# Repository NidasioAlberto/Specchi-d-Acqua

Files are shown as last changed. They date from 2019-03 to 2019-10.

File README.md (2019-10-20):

# Specchi d'Acqua

[Manifesto team Specchi d'Acqua](Manifesto_team_Specchi_d'Acqua.pdf)

[Modello su Prusa printers](https://www.prusaprinters.org/prints/7135-drone-acquatico)

## Presentazione del progetto

### Introduzione
Il progetto Specchi d’Acqua si pone l’obiettivo di aiutare gli scienziati nello
studio dei cambiamenti climatici. Proponiamo una rete di droni autonomi
che, spostandosi per i mari, monitorano i cambiamenti dovuti al riscaldamento
globale: dall’aumento delle temperature all'innalzamento del livello dell’acqua.
I droni sono in parte costruiti con elementi riciclati per diminuire il loro
impatto ambientale, nell’ottica del riutilizzo di materiali destinati al monouso.

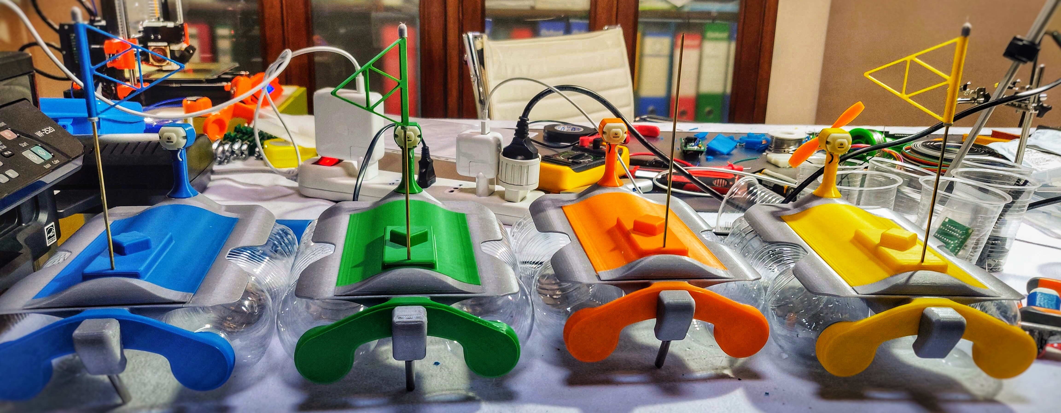
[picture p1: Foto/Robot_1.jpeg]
Robot

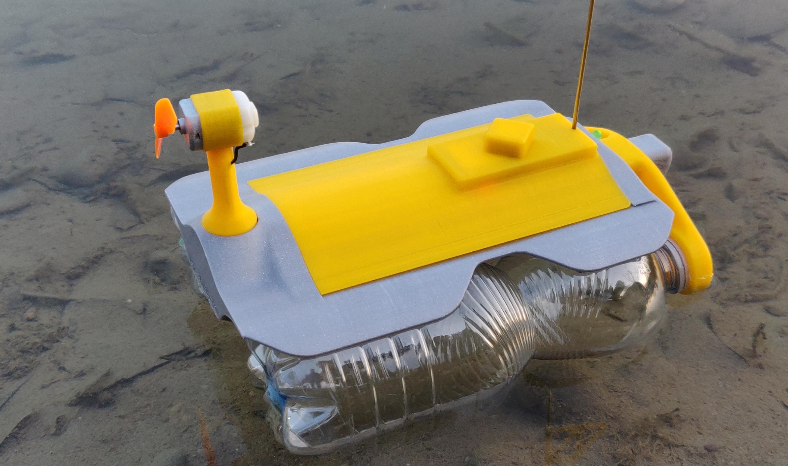
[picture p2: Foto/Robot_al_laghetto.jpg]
Robot al laghetto


**Video:** [prove dei robot](https://youtu.be/X26Ot0CG_ao)

### La squadra

**Video**: [presentazione team](https://youtu.be/9cNglWY3D-Q)

Alberto Nidasio e Matteo Cristini

### Il problema affrontato

**Video**: [Il cambiamento climatico è reale!](https://youtu.be/WMdsdqbVi9s)

Il cambiamento climatico è un grave problema che affligge il nostro pianeta e produce effetti devastanti, molte volte purtroppo imprevedibili, che già oggi possiamo constatare. Il mar Mediterraneo, ad esempio, essendo una zona chiusa sta sperimentando l’impatto di questi cambiamenti più di altre aree del pianeta.
Gli effetti prodotti sono svariati e l’aumento delle temperature (il 2018 è il quarto anno più caldo di sempre) ne è la causa principale. Tra i numerosi problemi c’è la riduzione delle precipitazioni, seppur controintuitiva, che comporta l’aumento della richiesta idrica, soprattutto per uso agricolo (si stima fino al 74%). Aumentano inoltre la diffusione delle malattie e i danni alla salute dovuti alle ondate di calore che ormai caratterizzano le nostre estati.
Il livello dei mari in tutto il mondo sta aumentando e le località costiere corrono un grande rischio. Invece le alte temperature danneggiano i coralli e alterano i delicati ecosistemi marini.
Lo studio da parte degli scienziati di tutti questi fenomeni interconnessi e altamente complessi si basa sulla disponibilità di dati e analisi il più possibile accurati e distribuiti al fine di poter, non solo capire il perché si sia verificato un fenomeno, ma anche per prevedere possibili disastri.

### La nostra soluzione

**Video**: [Presentazione del progetto](https://youtu.be/HUvQelgl1Qg)

La raccolta dati è fondamentale prima di ogni azione mirata: la si fa per un’analisi di mercato, per l’acquisto di un giocatore, perfino per un attacco informatico. Impiegarla per studiare i fenomeni naturali è però più complesso e costoso, infatti richiede attrezzature all’avanguardia non sempre recuperabili.
Noi abbiamo la soluzione! Il nostro progetto consiste in una flotta di droni acquatici, realizzati con materiali riciclati, in grado di distribuirsi in autonomia in un’area prestabilita, tornando alla base a fine missione. Grazie a un modulo GPS installato su ciascuno di essi, i robot potranno capire dove si trovano e mantenere la posizione nonostante le correnti. I droni potranno essere equipaggiati con diversi sensori per monitorare qualunque tipo di dato sia richiesto dagli analisti e, attraverso un sistema di comunicazione wireless, saranno in grado di trasmettere i dati in tempo reale alla base, associandoli con la posizione recuperata dal GPS.I prototipi che abbiamo preprato hanno molti aspetti innovativi. La costruzione dello scafo utilizza bottigliette di plastica e questo ci permette di recuperare quello che altrimenti sarebbe un rifiuto abbandonato.
Inoltre sia il codice che i design del robot saranno open-source permettendo così a chiunque di migliorare il progetto apportando nuove modifiche.
Il robot utilizza anche parti stampate in 3D. Questi componenti sono realizzati su misura, permettendo a ogni modello di essere equipaggiato con diversi sensori e batterie, per adattarsi alle esigenze del momento.

## Descrizione tecnica: drone

### Lo scafo

Il drone è composto da uno scafo realizzato con bottigliette di plastica tenuto assieme da una struttura progettata a **CAD** e realizzata con **stampante 3D**, adattabile in base alle esigenze e che contiene:
- i motori, per la propulsione e l'orientamento dell'elica;
- i sensori;
- il microcontrollore, che raccoglie i dati, gestisce la comunicazione e coordina il movimento;
- la sezione alimentazione che fornisce elettricità ai vari componenti.

I modelli del drone sono disponibili [qui](Modelli).

**Video:** [Esplosione modello](https://youtu.be/hAqc2swxTDc)

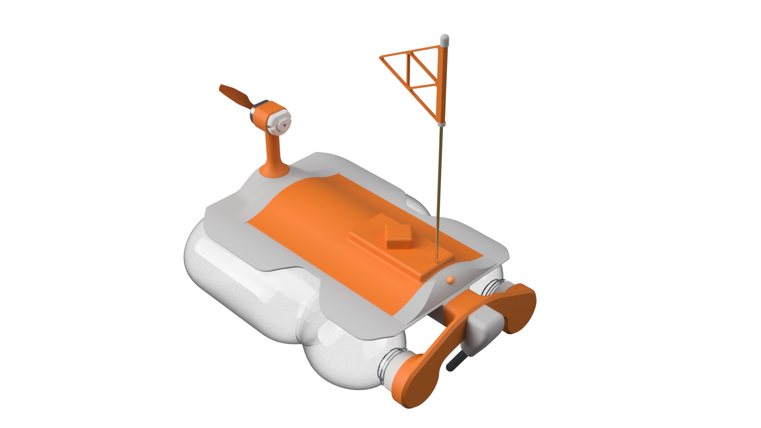
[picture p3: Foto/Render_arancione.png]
Foto modello


### Processore, sensori, alimentazione e schemi tecnici

La raccolta dei dati è gestita dal microcontrollore ESP8266 che è stato scelto per la sua disponibilità a un prezzo modesto e per le numerose funzionalità offerte. Infatti, non solo dispone di numerose porte I/O, ma anche di un trasmettitore wifi che metterà in comunicazione i droni tra di loro. Per quanto riguarda la scelta dei sensori, il progetto prevede piena libertà nella loro selezione in base alle esigenze del caso. Per questo prototipo abbiamo impiegato sensori di temperatura (sia in aria che in acqua, con una sonda da immergere), umidità e un modulo gps. Verrà quindi registrata la posizione del robot non solo per permettergli di distribuirsi nell’area designata, ma anche per associarla ai dati dei sensori.
Per l’elettronica di bordo sono stati previsti diversi metodi di alimentazione:
- tramite pile stilo da sostituire regolarmente (metodo attuale);
- tramite batteria ricaricabile al litio: è previsto siano necessarie due celle
assieme a un circuito di ricarica dedicato; Sul coperchio è possibile installare un pannello solare di dimensioni contenute in grado di ricaricare il gruppo batterie del robot.

#### Processore e sensori

L'Esp8266 ci permette di utilizzare i sensori **DHT11** (temperatura e umidità aria), **DS18B20** (Sonda temperatura acqua) e il modulo gps **GT-U7**. Per collegare tutti questi componenti abbiamo preparato una scheda millefori che verrà alloggiata nel coperchio dello scafo per una manutenzione facile e semplice. Una volta finalizzato il design potremo creare un vera e propria **PCB** con componenti **SMT**.

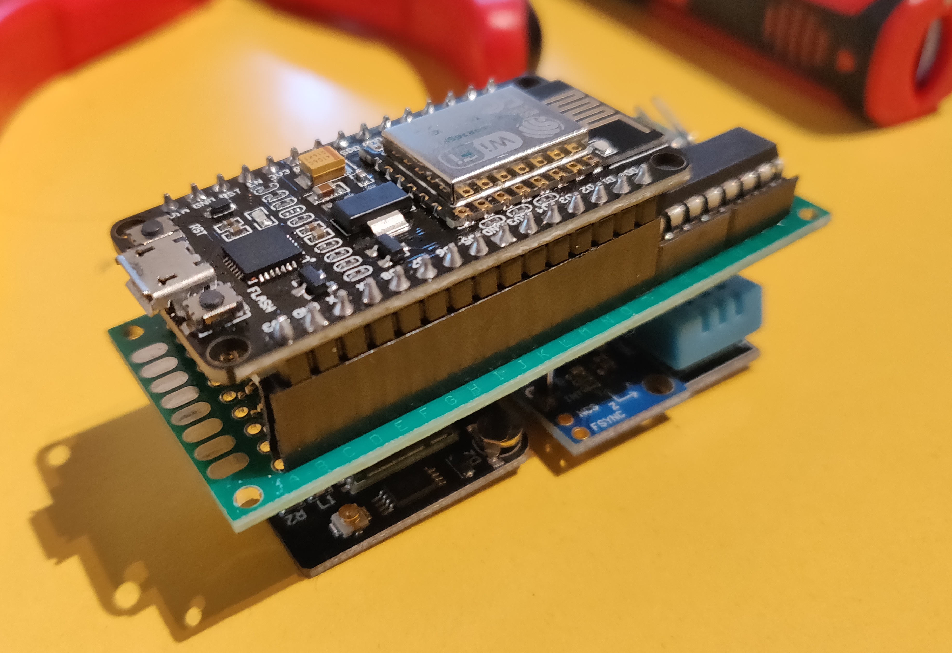
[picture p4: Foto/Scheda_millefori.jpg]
Scheda millefori


#### Alimentazione

Per alimentare la scheda e i motori abbiamo utilizzato due set di batterie separati. Il primo, composto da 4 batteria AA fornisce elettricità al motore DC che muove l'elica, e il secondo, formato da 6 batterie AAA, che alimenta l'elettronica e il motore passo passo che inclina l'elica.
Questo evita che, nel caso di cali di tensione all'elettronica dovuti all'avvio del motore o se si scaricano le batterie del motore DC, il drone perda il segnale e non risponda più ai programmi.

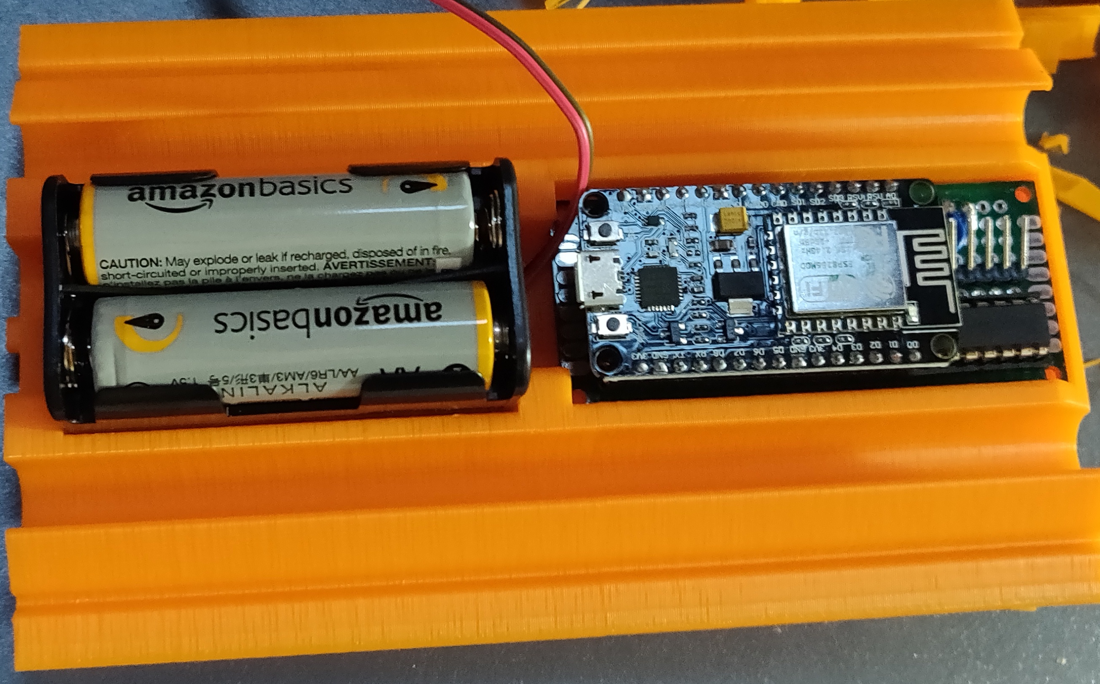
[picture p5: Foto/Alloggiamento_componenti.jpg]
Foto alloggiamento batterie


#### Schemi tecnici

![Schema millefori]()

## Descrizione tecnica: collettore

I droni, distribuite su una vasta zona, avranno bisogno di un sistema di comunicazione affidabile a lunga distanza. In base alle dimensioni dell’area su cui devono essere distribuiti abbiamo valutato diverse soluzioni:
- Per comunicazioni nell’ordine delle decine di chilometri sono disponibili moduli **LoRa** (Long Range), anche ad un prezzo ridotto, che permettono un collegamento a maglia, estendendo così considerevolmente la rete, a patto che ci sia un numero sufficiente di nodi.
- Nel caso invece si voglia lavorare su zone più ampie, esigendo anche un livello di affidabilità superiore, si potrà sfruttare, nei prossimi anni, la rete satellitare **Starlink**, una costellazione di 12.000 satelliti che SpaceX sta sviluppando per portare l’accesso ad internet in qualunque area del pianeta. Questo offrirebbe una connessione indipendente per ciascun drone eliminando la possibilità che alcuni possano rimanere isolati.

Per il prototipo abbiamo utilizzato una rete **Wifi** che collega droni e collettore con la possibilità di essere estesa con dei ripetitori. Lo stesso sistema che abbiamo sviluppato, che utilizza il protocollo **MQTT** (per l'invio dei dati)  e **TCP** (per il controllo da remoto), potrà essere implementat con la rete cellurare.

Per il collettore, ovvero il server a terra che memorizza i dati, abbiamo utilizzato un **Raspberry pi**.

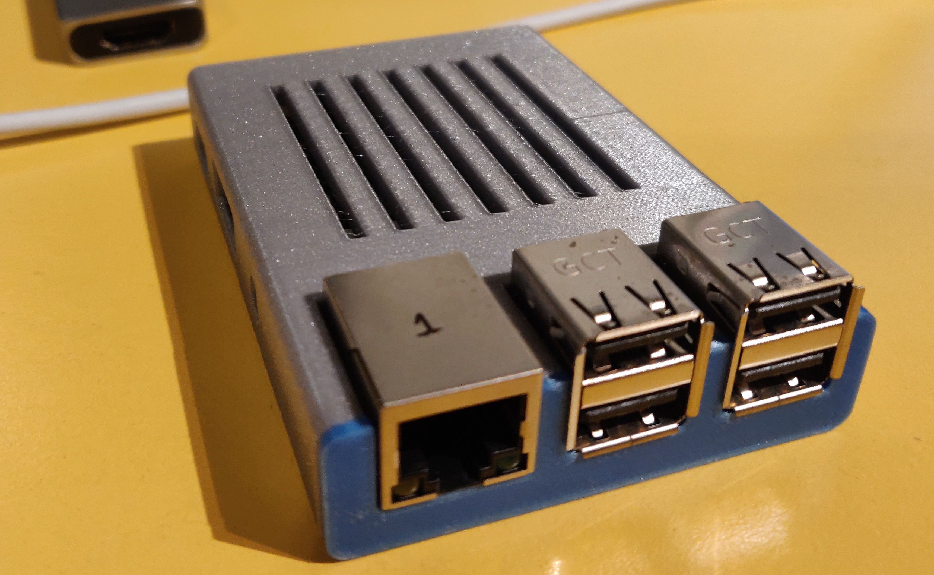
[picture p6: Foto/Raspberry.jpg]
Foto raspberry


## Software

Il collettore (S.O. Linux) implementa un broker **Mosquitto**, un server **Sql**, un server **HTTP** con un sito web e un processo per sincronizzare i dati web che forniscono i servizi necessari per la comunicazione, il salvataggio e la visualizzazione dei dati.

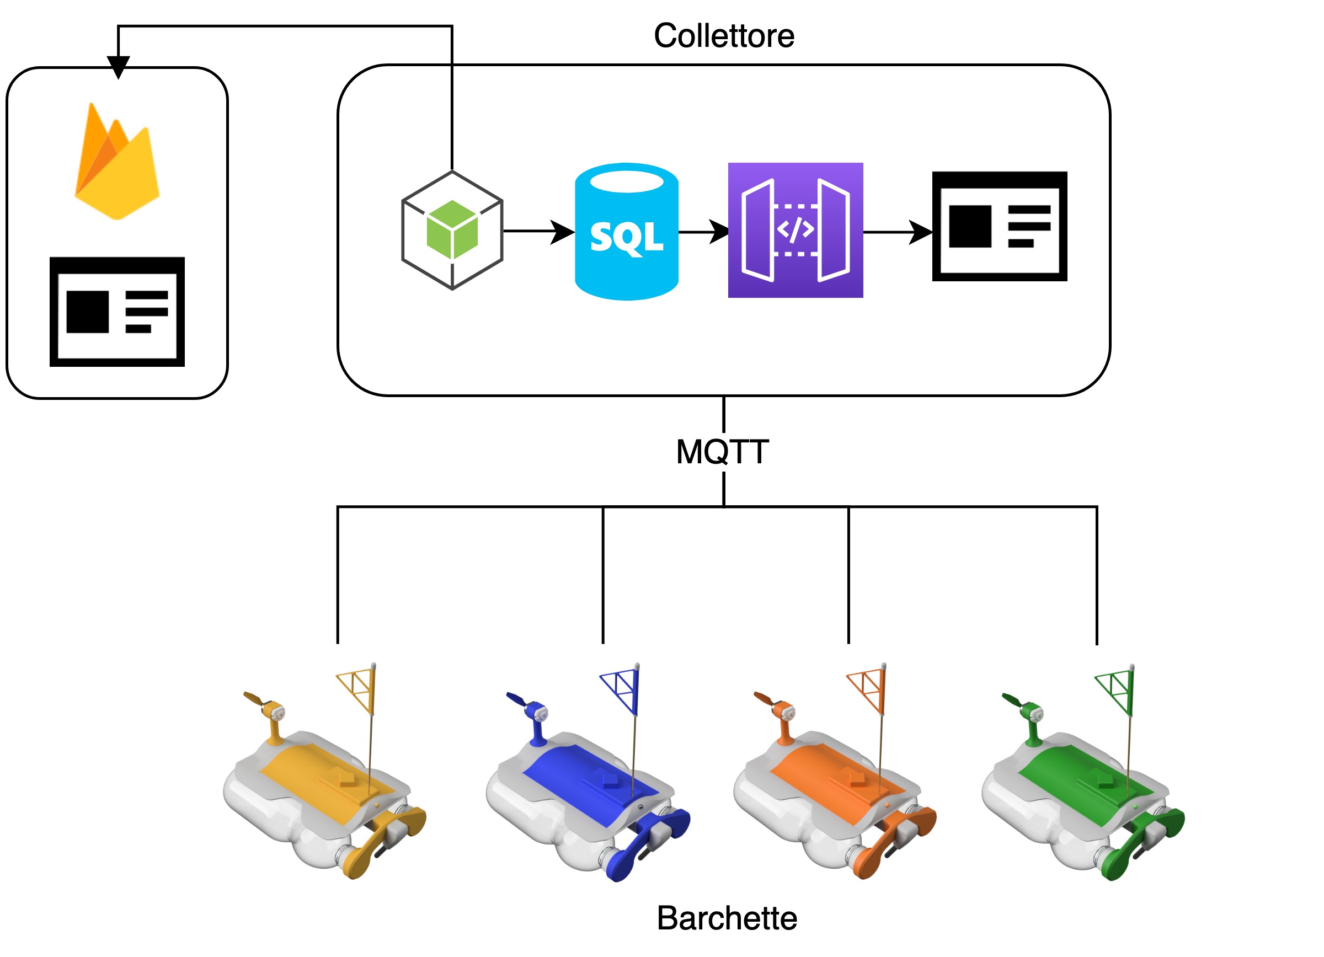
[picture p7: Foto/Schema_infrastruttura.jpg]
Schema imfrastruttura


### Broker Mosquitto

Per la comunicazione tra droni e collettore abbiamo utilizzato il protocollo ***MQTT*** che ci permette un'affidabilità della comunizatione superiore (QOS 2) e riduzione della dimensione dei messaggi. Questo è fornito dal popolare broker **Mosquitto** a cui si collegheranno i droni come publisher e il server.

### Server SQL

Il server **SQL** (MariaDB) è organizzato in 4 tabelle principali:
- **Droni**: contiene la lista di tutte i droni prodotti;
- **Sensori**: la lista di tutti i sensori utlizzati (esclusi GPS e bussola);
- **Record**: dove vengono salvati i dati principali di un record come posizione, data, ora e id del drone;
- **Dati sensori**: permette di memorizzare i valori di ciascun sensore rilevati in un record (questa è una tabella separata perchè i droni potrebbero non avere tutti la stessa configurazione).

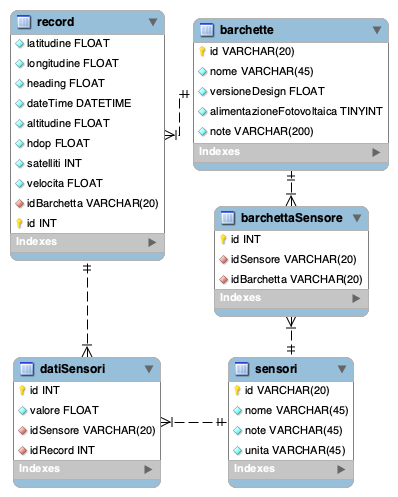
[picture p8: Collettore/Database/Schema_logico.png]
Schema logico


### Server HTTP

Questo servizio fornisce delle **API REST** che il sito web, sempre messo a disposizione da questo server, utilizza per mostrare i dati.

## Olimpiadi

### Giorno 1
**Video:** [time-lapse giorno 1](https://youtu.be/L8EZxuS9RvE), [time-lapse giorno 2](https://youtu.be/6cRvtolq8c4)

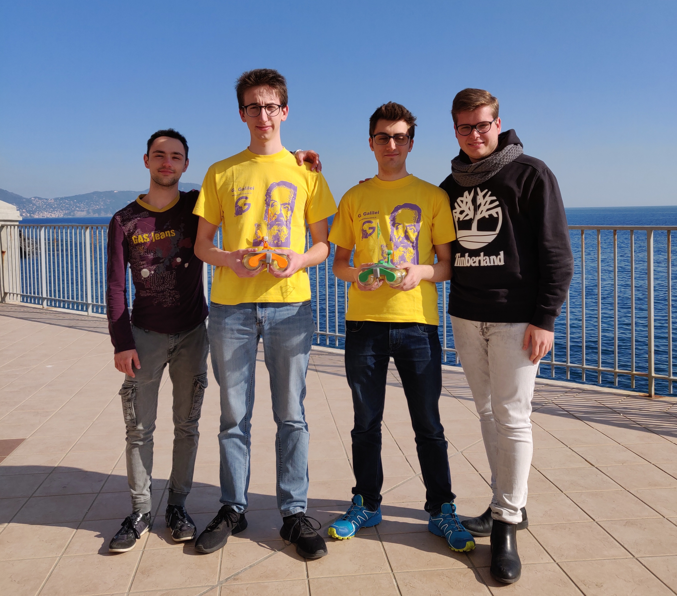
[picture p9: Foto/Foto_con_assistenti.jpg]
Foto con amici


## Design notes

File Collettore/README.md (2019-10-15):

# Impostazione raspberry collettore

## Setup access point

Per impostare il raspberry come access point è possibile seguire questa guida: [Tutorial](https://www.raspberrypi.org/documentation/configuration/wireless/access-point.md)

## Setup MQTT - server mosquitto

[Tutorial](https://appcodelabs.com/introduction-to-iot-build-an-mqtt-server-using-raspberry-pi)

## Setup server SQL

[Tutorial](https://pimylifeup.com/raspberry-pi-mysql/)

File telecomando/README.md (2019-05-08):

# telecomando

A new Flutter project.

## Getting Started

This project is a starting point for a Flutter application.

A few resources to get you started if this is your first Flutter project:

- [Lab: Write your first Flutter app](https://flutter.io/docs/get-started/codelab)
- [Cookbook: Useful Flutter samples](https://flutter.io/docs/cookbook)

For help getting started with Flutter, view our 
[online documentation](https://flutter.io/docs), which offers tutorials, 
samples, guidance on mobile development, and a full API reference.

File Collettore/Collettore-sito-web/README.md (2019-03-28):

# CollettoreSitoWeb

This project was generated with [Angular CLI](https://github.com/angular/angular-cli) version 7.3.4.

Aggiunta la lib. angular material
Aggiunta la lib. angularfire2
Aggiunta la lib. ng2chart
Aggiunta la lib. chart.js

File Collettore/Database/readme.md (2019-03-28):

# Database barchette
Alberto Nidasio - Stefano Vassallo

[PDF presentazione 😄](Presentazione_database_barchette.pdf)

## Problema da risolvere
Il team Specchi d’Acqua, che parteciperà alle prossime olimpiadi di robotica a Genova, ha bisogno di salvare i dati ambientali raccolti dalle proprie barchette (temperatura, umidità, ecc...).

## Casi d'uso
Casi d'uso

## Struttura della soluzione
- Database
- Server REST
- Sito web

## Schema database
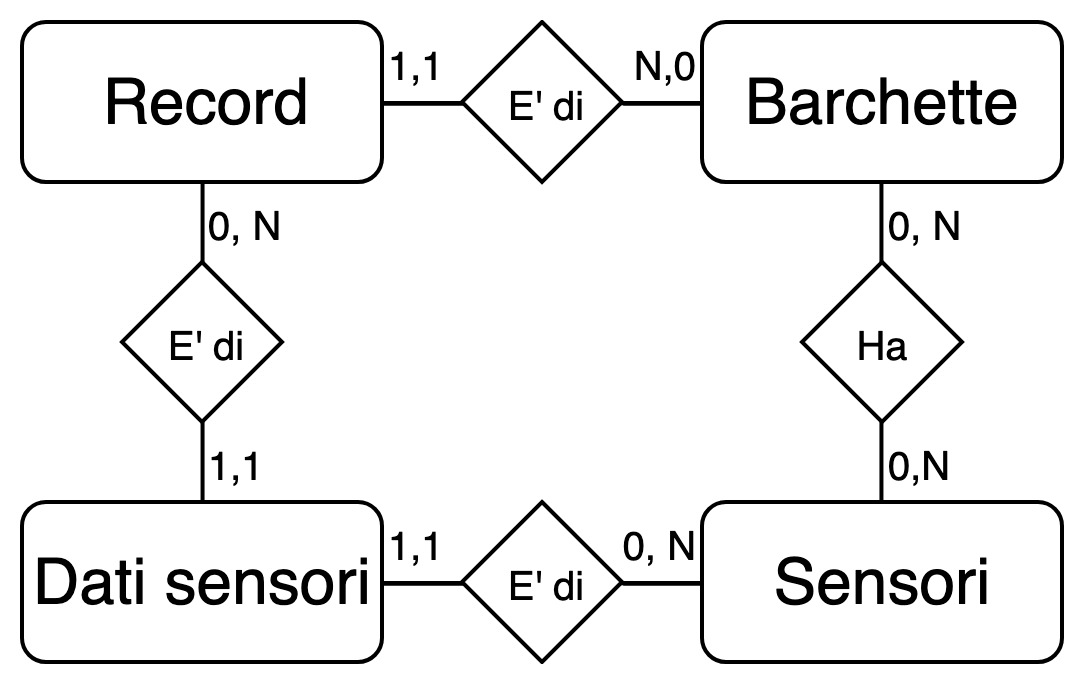
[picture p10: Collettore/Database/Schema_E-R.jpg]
Schema E/R

Schema logico

## Codice server
Utilizzo di NodeJs per l'applicazione server che, oltre alle API REST mette a disposizione il sito web

[Esempio codice server](Server/server.ts)
```typescript
//preparo express
const app = express()
app.use(express.json())
app.use(cors({origin: '*'}))

//rendo disponibile la pagina web nella root dell'url
app.use('/', express.static('website'))

//SEZIONE RECORD

//lista record con i dati dei sensori
app.get('/api/record', async (req, res) => {
    console.log(req.method, req.url, req.query, req.body)

    try {
        return res.send(await database.ottieniRecord(req.query.limite))
    } catch(errore) {
        return res.status(500).send(errore.message)
    }
})
```

## Codice client
Pagina web realizzata con Boostrap e JQuery

[Esempio metodo GET](Server/website/code.js)
```javascript
//funzione per caricare le barchette nella tabella
function caricaBarchette() {
    const http = new XMLHttpRequest()
    const url = 'http://localhost/api/barchette'
    http.open('GET', url)
    http.onload = (e) => {
        var data = JSON.parse(http.responseText)
        $('#tabella-barchette').bootstrapTable({
            columns: [{
                    field:'id',
                    title: '#'
                }, {
                    field:'nome',
                    title: 'Nome'
                }, {
                    field:'versioneDesign',
                    title: 'V. Design'
                }, {
                    field:'alimentazioneFotovoltaica',
                    title: 'Fotovoltaico'
                }, {
                    field:'note',
                    title: 'Note'
                }],
            data
        })
    }
    http.send()
}
```
[Esempio metodo POST](Server/website/code.js)
```javascript
//funzione per registrare un nuovo sensore
function aggiungiSensore() {
    let id = document.getElementById('sensore-id').value
    let nome = document.getElementById('sensore-nome').value
    let note = document.getElementById('sensore-nota').value
    let unita = document.getElementById('sensore-unita').value

    //controllo i dati
    if(id == '' || nome == '' || note == '' || unita == '') {
        //mostro un avviso all'utente
        alert('Compilare tutti i campi!')
    } else{
        const http = new XMLHttpRequest()
        const url = 'http://localhost/api/sensori'
        http.open('POST', url)
        http.setRequestHeader('Content-Type', 'application/json')

        var sensore = { id, nome, note, unita }

        http.onload = (e) => {
            document.getElementById('sensore-id').value = ''
            document.getElementById('sensore-nome').value = ''
            document.getElementById('sensore-nota').value = ''
            document.getElementById('sensore-unita').value = ''
        }

        http.send(JSON.stringify(sensore))
    }	
}
```

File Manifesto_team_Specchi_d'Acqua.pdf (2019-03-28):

# Missione: Specchi d'Acqua

Scuola: IIS G. Galilei Crema Docente Coach: Lini Patrizia Nome Squadra: Specchi d’Acqua di Cristini Matteo, Nidasio Alberto

Ambiente di intervento: Acqua Link al video: Presentazione della Squadra (https://www.youtube.com/watch?v=9cNglWY3D-Q&list=PL8SoLGSAr36Su3RwwoVQFDCZ6iDOUV9Au&index=2) Link al video: Presentazione del Problema (https://youtu.be/WMdsdqbVi9s) Link al video: Presentazione del Progetto (https://youtu.be/HUvQelgl1Qg)

Indice dei contenuti

- Introduzione e vincoli di progetto
- Presentazione del problema da risolvere
- Descrizione della soluzione
- Presentazione del robot
- Schemi tecnici
- Elettronica
- Programmazione
- Conclusioni

Introduzione
Il progetto Specchi d’Acqua si pone l’obiettivo di aiutare gli scienziati nello studio dei cambiamenti climatici. Proponiamo una rete di barche autonome che, spostandosi per i mari, monitorano i cambiamenti dovuti al riscaldamento globale: dall’aumento delle temperature all'innalzamento del livello dell’acqua. Le barche sono in parte costruite con elementi riciclati per diminuire il loro impatto ambientale, nell’ottica del riutilizzo di materiali destinati al monouso.

Presentazione del problema da risolvere
Il cambiamento climatico è un grave problema che affligge il nostro pianeta e produce effetti devastanti, molte volte purtroppo imprevedibili, che già oggi possiamo constatare. Il mar Mediterraneo, ad esempio, essendo una zona chiusa sta sperimentando l’impatto di questi cambiamenti più di altre aree del pianeta.
Gli effetti prodotti sono svariati e l’aumento delle temperature (il 2018 è il quarto anno più caldo di sempre) ne è la causa principale. Tra i numerosi problemi c’è la riduzione delle precipitazioni, seppur controintuitiva, che comporta l’aumento della richiesta idrica, soprattutto per uso agricolo (si stima fino al 74%). Aumentano inoltre la diffusione delle malattie e i danni alla salute dovuti alle ondate di calore che ormai caratterizzano le nostre estati. Il livello dei mari in tutto il mondo sta aumentando e le località costiere corrono un grande rischio. Invece le alte temperature danneggiano i coralli e alterano i delicati ecosistemi marini.
Lo studio da parte degli scienziati di tutti questi fenomeni interconnessi e altamente complessi si basa sulla disponibilità di dati e analisi il più possibile accurati e distribuiti al fine di poter, non solo capire il perché si sia verificato un fenomeno, ma anche per prevedere possibili disastri.

Descrizione della soluzione
La raccolta di dati è fondamentale prima di ogni azione mirata: la si fa per un’analisi di mercato, per l’acquisto di un giocatore, perfino per un attacco informatico. Impiegarla per studiare i fenomeni naturali è però più complesso e costoso, infatti richiede attrezzature all’avanguardia non sempre recuperabili.
Noi abbiamo la soluzione! Ed è la migliore per raccogliere dati ambientali sui mari. Il nostro progetto consiste in una flotta di droni acquatici, realizzati con materiali riciclati, in grado di distribuirsi in autonomia in un’area prestabilita, tornando alla base a fine missione. Grazie a un modulo GPS installato su ciascuno di essi, i robot potranno capire dove si trovano e mantenere la posizione nonostante le correnti. I droni potranno essere equipaggiati con diversi sensori per monitorare qualunque tipo di dato sia richiesto dagli analisti e, attraverso un sistema di comunicazione wireless, saranno in grado di trasmettere i dati in tempo reale alla base, associandoli con la posizione recuperata dal GPS.

Presentazione del robot
Come detto al punto precedente stiamo realizzando una flotta di droni il cui obiettivo principale è quello di aiutare nella raccolta dati. I prototipi che stiamo preparando hanno molti aspetti innovativi. La costruzione dello scafo utilizza bottigliette di plastica e questo ci permette di recuperare quello che altrimenti sarebbe un rifiuto abbandonato.
Inoltre sia il codice che i design del robot saranno open-source permettendo così a chiunque di migliorare il progetto apportando nuove modifiche.
Il robot utilizza anche parti stampate in 3D. Questi componenti sono realizzati su misura, permettendo a ogni modello di essere equipaggiato con diversi sensori e batterie, per adattarsi alle esigenze del momento.
La guida è autonoma; i droni, una volta “liberati”, si distribuiscono e iniziano la raccolta dati, comunicando le letture dei sensori a un concentratore che si trova a terra, responsabile poi dell’immagazzinamento dei dati e della loro analisi.

Schemi tecnici
Lo schema tecnico proposto rappresenta una versione provvisoria dei componenti dell’elettronica di bordo.

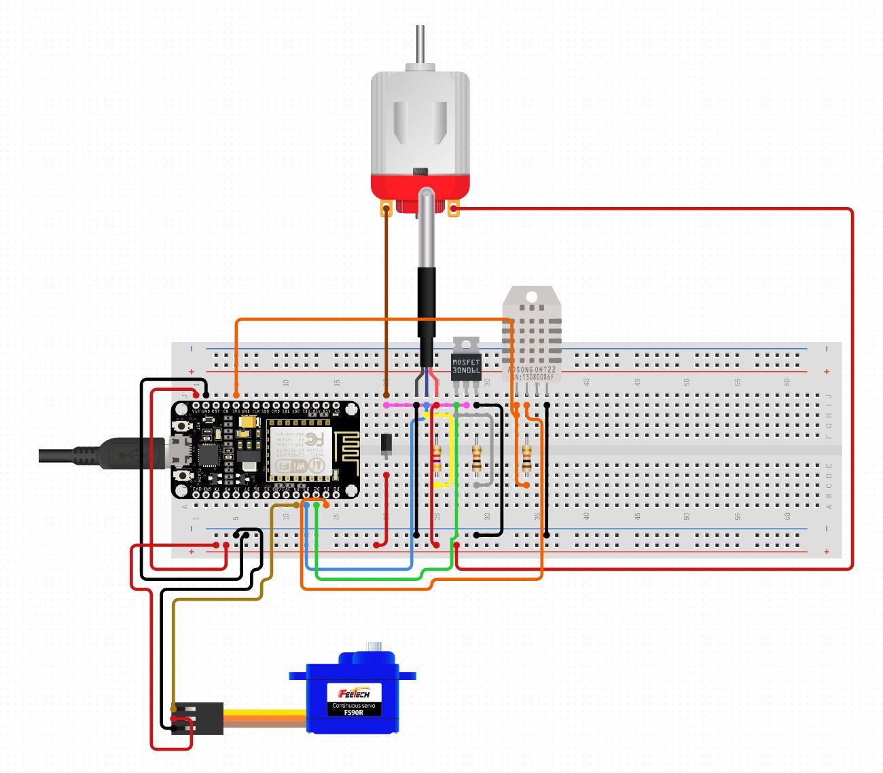
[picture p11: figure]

Elettronica e costruzione - Lo scafo
Il drone è composto da uno scafo realizzato con bottigliette di plastica tenuto assieme da una struttura realizzata con stampante 3D, adattabile in base alle esigenze e che contiene:
- i motori, per la propulsione e il timone;
- i sensori;
- il microcontrollore, che raccoglie i dati,

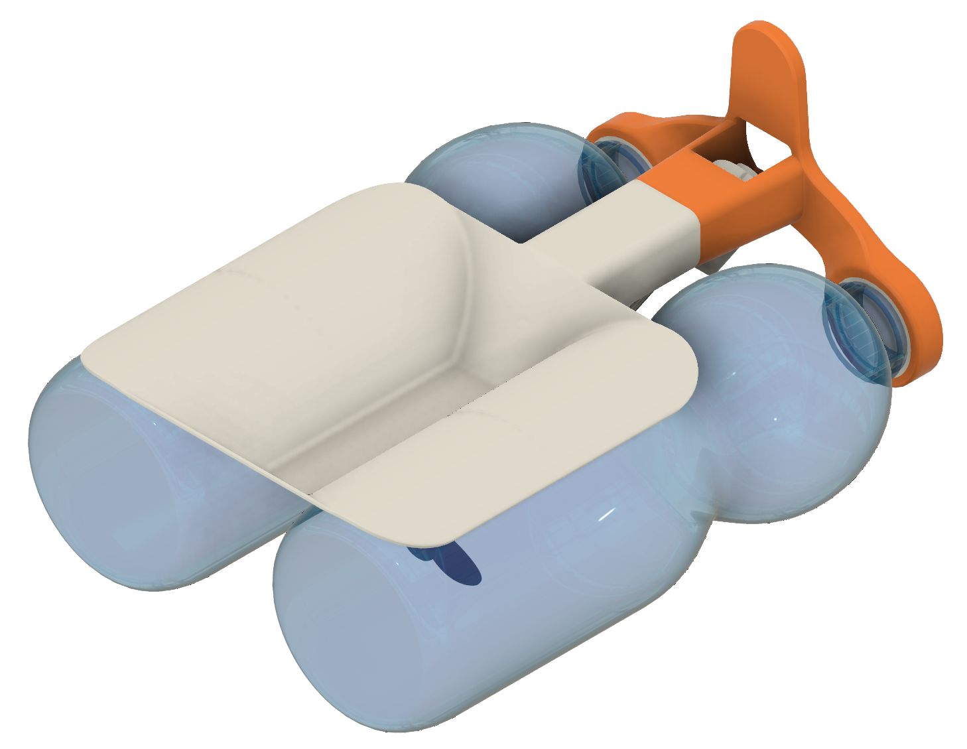
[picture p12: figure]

gestisce la comunicazione e coordina il movimento;
- la sezione alimentazione che procura elettricità ai vari componenti e ricarica le batterie con pannelli fotovoltaici.

Elettronica e costruzione - Processore e
sensori
La raccolta dei dati è gestita dal microcontrollore ESP8266 che è stato scelto per la sua disponibilità a un prezzo modesto e per le numerose funzionalità offerte.
Infatti, non solo dispone di numerose porte
I/O, ma anche di un trasmettitore wifi che
metterà in comunicazione i droni tra di loro.

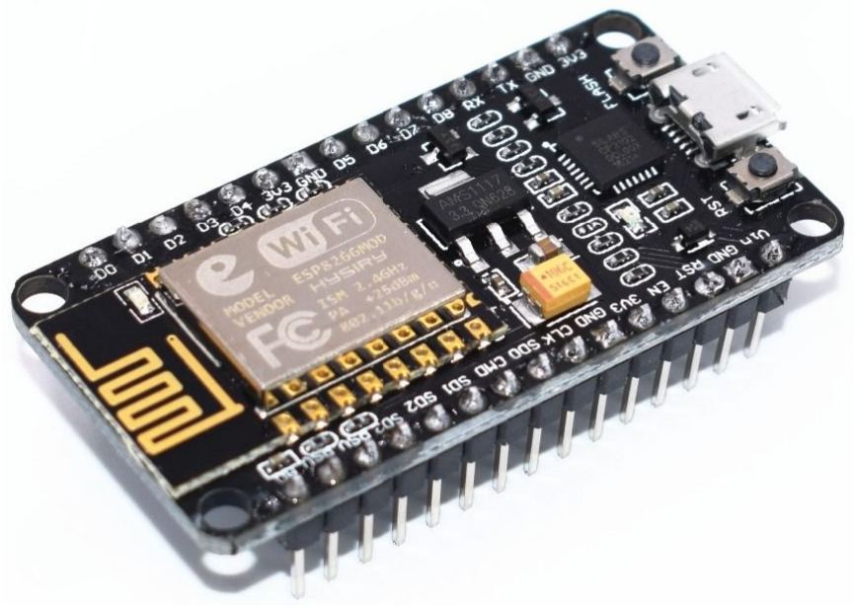
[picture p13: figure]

Per quanto riguarda la scelta dei sensori, il progetto prevede piena libertà nella loro selezione in base alle esigenze del caso. Per i primi prototipi e test verranno impiegati sensori di concentrazione CO2 e di temperatura (sia in aria che in acqua, con una sonda da immergere) mentre sono necessari due moduli: bussola e gps.
Verrà quindi registrata la posizione del robot non solo per permettergli di distribuirsi nell’area designata, ma anche per associarla ai dati dei sensori.

Elettronica e costruzione - Alimentazione
Per l’elettronica di bordo sono stati previsti diversi metodi di alimentazione:
- tramite quattro pile stilo da sostituire regolarmente;
- tramite batteria ricaricabile al litio: è previsto siano necessarie due celle assieme a un circuito di ricarica dedicato.

Sulla piattaforma dei sensori è possibile installare un pannello solare di dimensioni contenute in grado di ricaricare il gruppo batterie del robot.

Programmazione, codice e comunicazione
I droni marini, distribuiti su una vasta zona, avranno bisogno di un sistema di comunicazione affidabile a lunga distanza. In base alle dimensioni dell’area su cui devono essere distribuiti abbiamo valutato diverse soluzioni.
Per comunicazioni nell’ordine delle decine di chilometri sono disponibili moduli LoRa (Long Range), anche ad un prezzo ridotto, che permettono un collegamento a maglia, estendendo così considerevolmente la rete, a patto che ci sia un numero sufficiente di droni.
Nel caso invece si voglia lavorare su zone più ampie, esigendo anche un livello di affidabilità superiore, si potrà sfruttare, nei prossimi anni, la rete satellitare Starlink, (https://en.wikipedia.org/wiki/Starlink_(satellite_constellation)) una costellazione di 12.000 satelliti che SpaceX sta sviluppando per portare l’accesso ad internet in qualunque area del pianeta. Questo offrirebbe una connessione indipendente per ciascun drone eliminando la possibilità che alcuni possano rimanere isolati.

Conclusioni
Il cambiamento del nostro pianeta è reale e solo un attento studio dei fenomeni e dell’ambiente ci permetterà di capire e prevenire numerosi disastri. In questo la tecnologia è il miglior alleato che si possa avere dalla propria parte e noi del team “Specchi d’Acqua”, sentendo molto questo problema, ci proponiamo di sfruttare i nostri studi odierni e futuri per contribuire alla salvaguardia del patrimonio di bellezze che la terra offre.

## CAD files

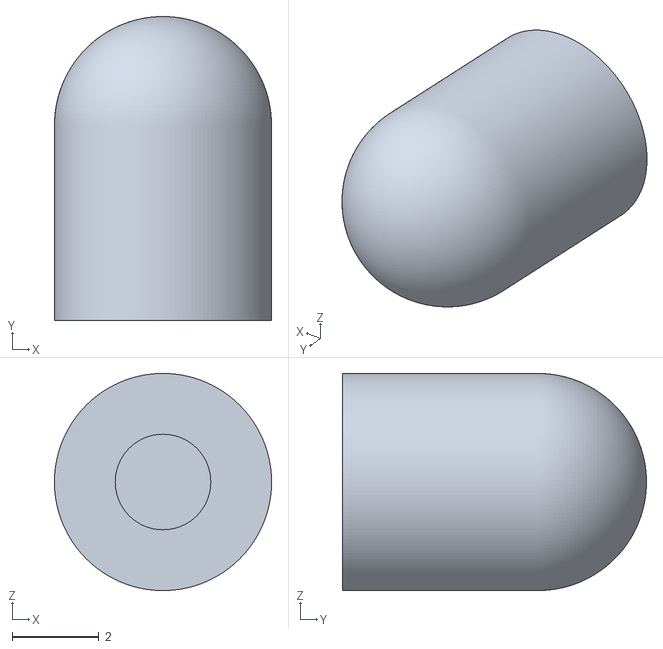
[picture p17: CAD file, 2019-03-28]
Modelli/Parti/Supporto superiore bandierina.stl
5.00 x 7.00 x 5.00

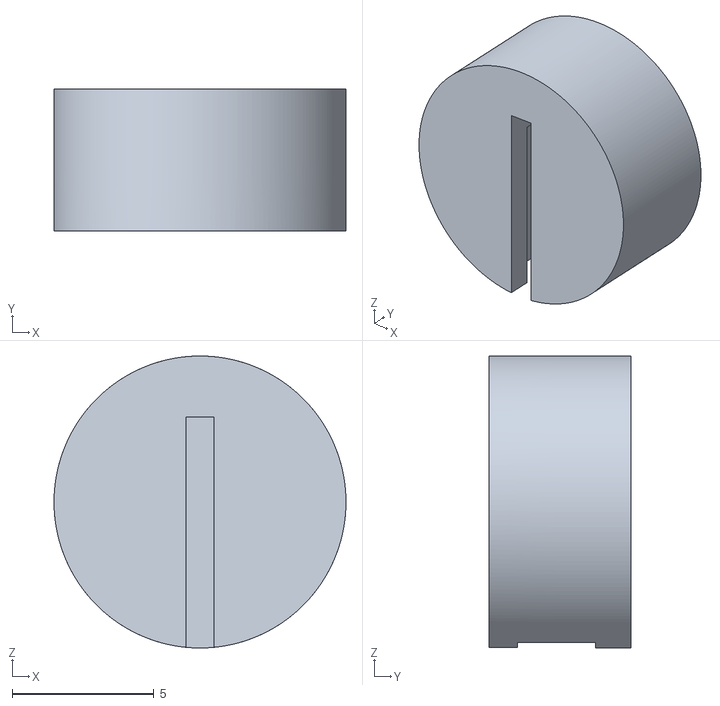
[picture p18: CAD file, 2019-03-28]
Modelli/Parti/Contatto batterie AAA pt1.stl
10.3 x 5.00 x 10.3

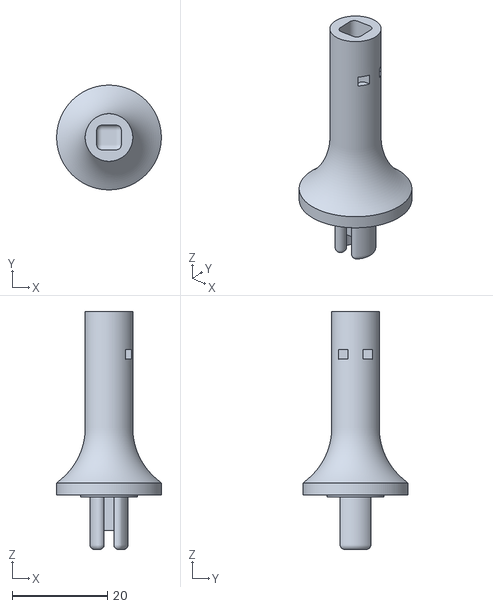
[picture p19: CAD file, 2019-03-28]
Modelli/Parti/Asse motore.stl
22.0 x 22.0 x 50.0

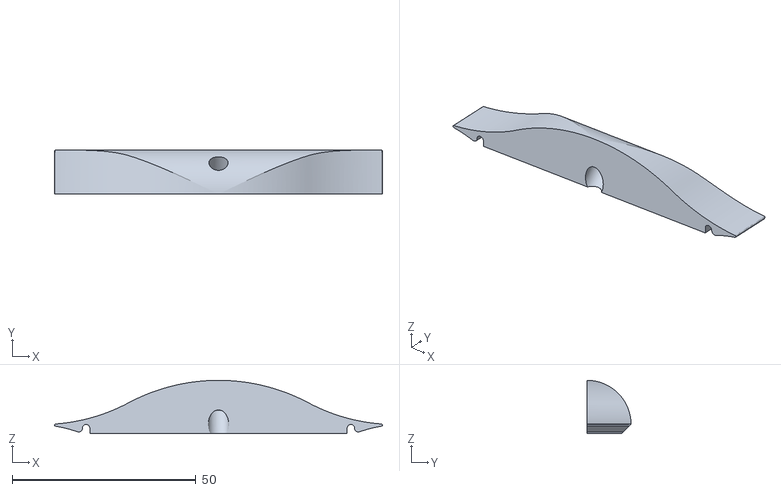
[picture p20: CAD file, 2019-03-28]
Modelli/Parti/Supporto coperchio.stl
89.2 x 12.0 x 14.5

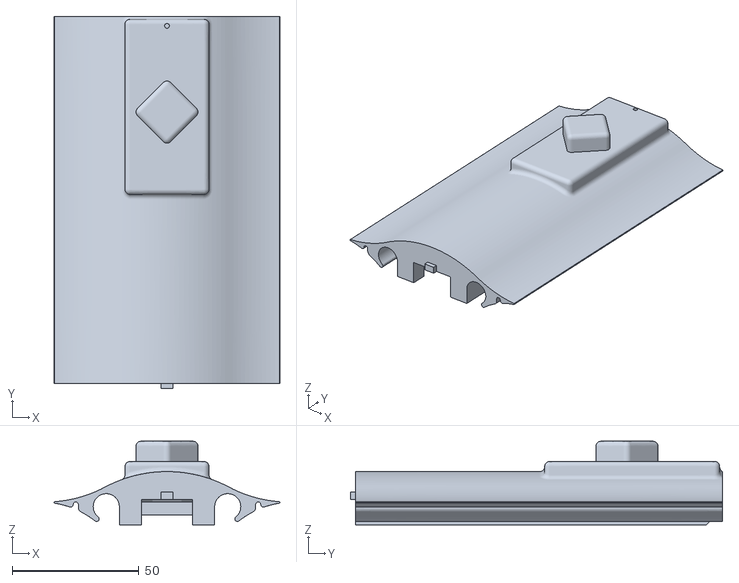
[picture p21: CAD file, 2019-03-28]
Modelli/Parti/Coperchio.stl
89.2 x 147.0 x 33.0

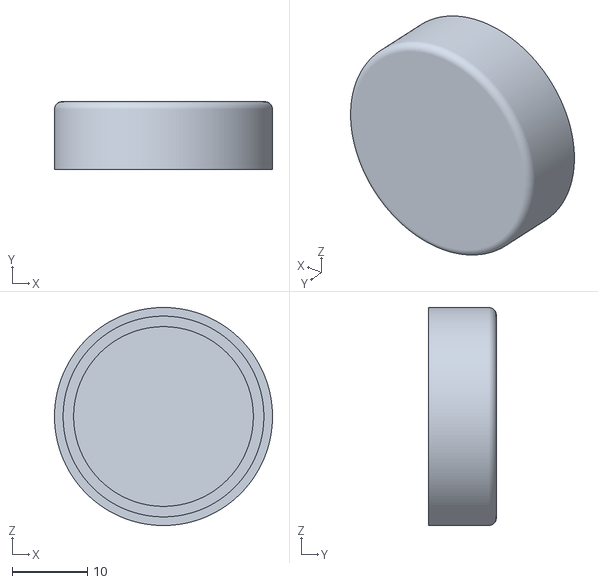
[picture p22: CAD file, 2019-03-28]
Modelli/Parti/Tappo.stl
29.0 x 9.00 x 29.0

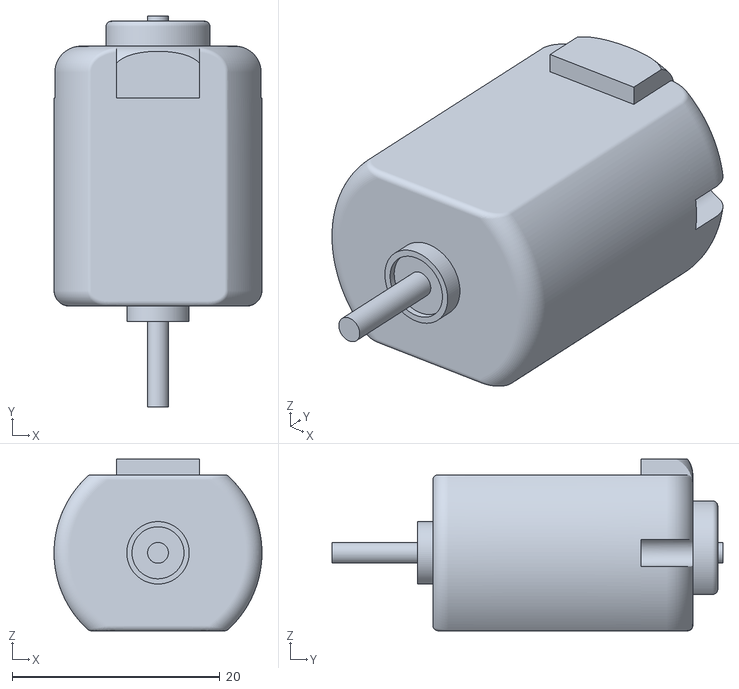
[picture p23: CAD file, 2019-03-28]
Modelli/Parti/Motore DC 3-6V v1.stl
20.0 x 37.6 x 16.5

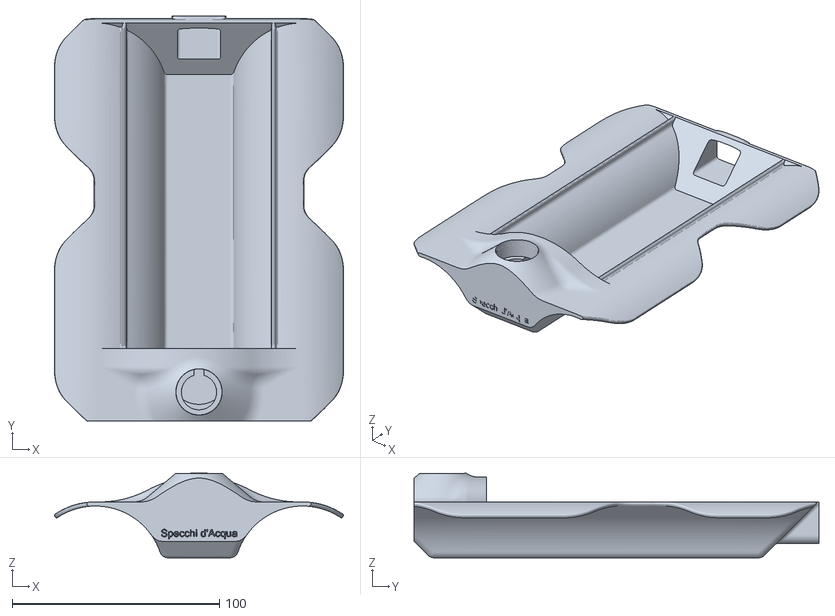
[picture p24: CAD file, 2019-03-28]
Modelli/Parti/Corpo centrale.stl
139.6 x 195.5 x 40.9

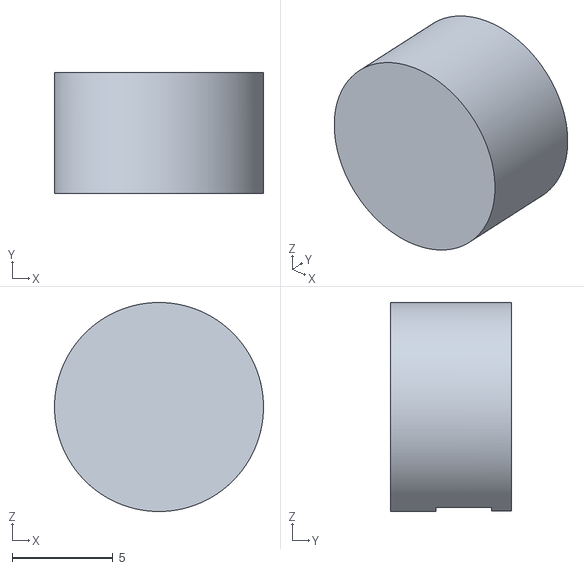
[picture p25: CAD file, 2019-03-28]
Modelli/Parti/Contatto batterie AAA pt2.stl
10.4 x 6.00 x 10.4

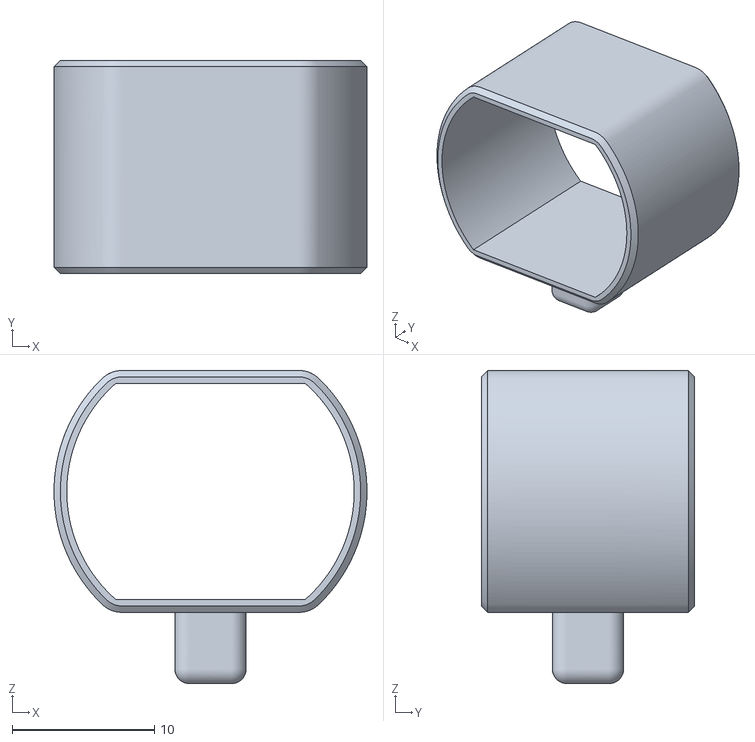
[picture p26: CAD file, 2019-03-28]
Modelli/Parti/Supporto motore.stl
22.0 x 15.0 x 22.0

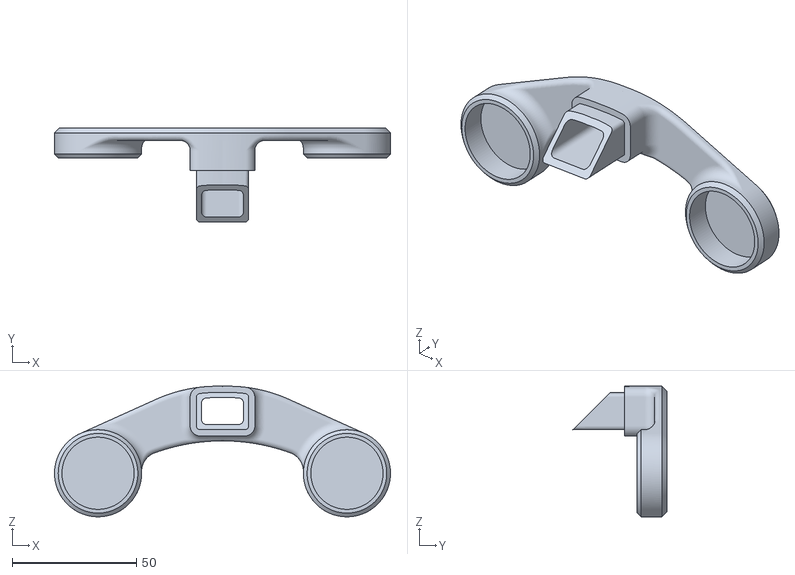
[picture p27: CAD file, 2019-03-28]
Modelli/Parti/Supporto bottiglie.stl
135.0 x 37.8 x 52.5

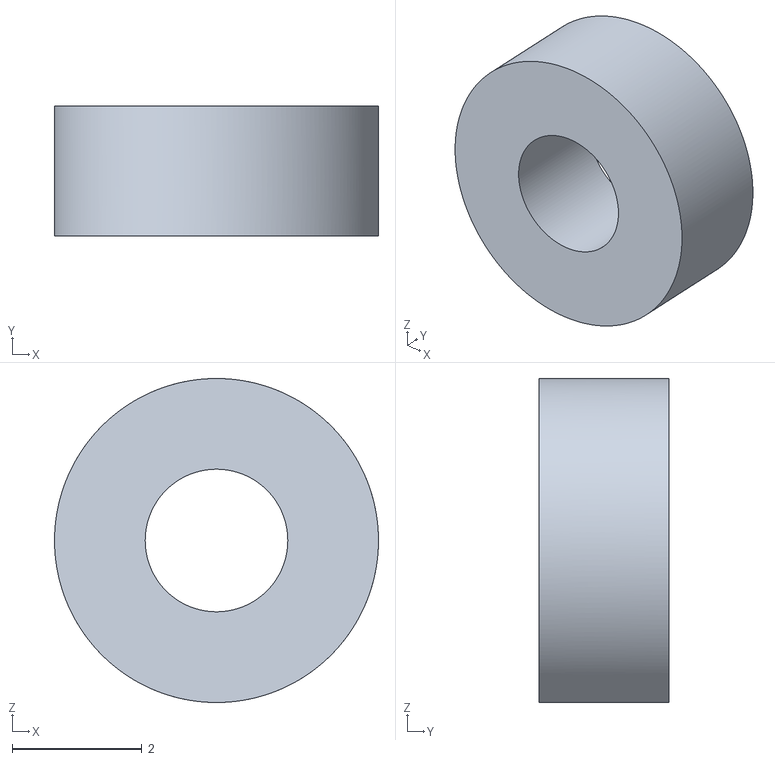
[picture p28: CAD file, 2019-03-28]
Modelli/Parti/Supporto inferiore bandierina.stl
5.00 x 2.00 x 5.00

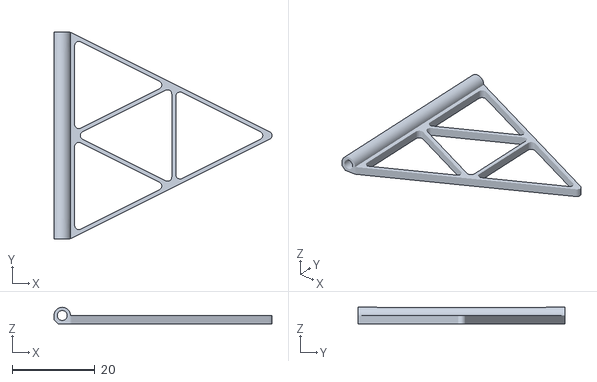
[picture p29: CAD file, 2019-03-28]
Modelli/Parti/Bandierina.stl
52.8 x 50.0 x 4.00

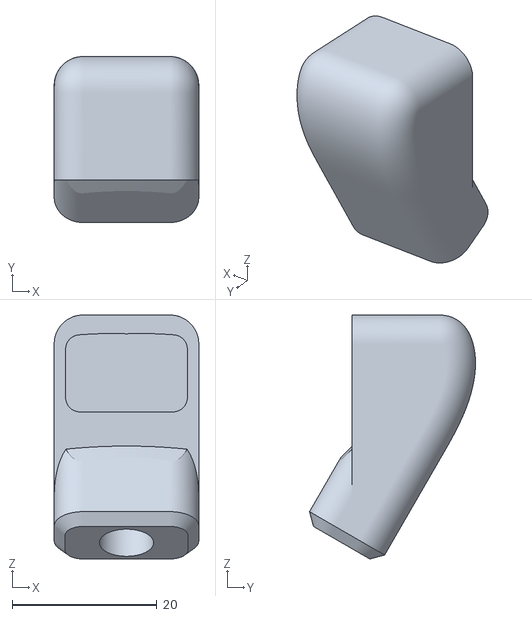
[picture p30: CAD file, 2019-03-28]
Modelli/Parti/Supporto sonda pt1.stl
20.0 x 23.0 x 33.7

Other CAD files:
Modelli/Parti/Supporto sonda pt2.stl
Modelli/Specchi d'acqua - design V1.f3d

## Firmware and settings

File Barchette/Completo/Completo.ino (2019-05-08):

/*
La versione corrente del programma prevede l'invio dei dati (sensori, gps e tensione batteria)
a una certa frequenza stabilita.
Inoltre accetta una connessione tcp sulla porta 1234 per il controllo remoto tramite app.
*/

//SEZIONE LIBRERIE

//Wifi
#include <ESP8266WiFi.h>
#include <PubSubClient.h>

//Probe
#include <OneWire.h>
#include <DallasTemperature.h>

//DHT11
#include <DHT.h>

//GPS
#include <TinyGPS++.h>
#include <SoftwareSerial.h>

//JSON
#include <ArduinoJson.h>
const size_t capacity = JSON_ARRAY_SIZE(3) + 3*JSON_OBJECT_SIZE(2) + JSON_OBJECT_SIZE(9) + 180;

//SEZIONE VARIABILI

//Wifi e connessioni
#define WIFI_SSID "Team_specchi"
#define WIFI_PSW "Fornaroli"
#define TCP_SERVER_PORT 1234

WiFiServer server(TCP_SERVER_PORT);
WiFiClient client, espClient;
PubSubClient mqtt(espClient);
boolean velocitaC, angoloC, direzioneC; //dati del telecomando
String velocita, angolo, direzione;

//Impostazioni MQTT
#define MQTT_USR "barca4"
#define MQTT_PSW "barca4"
#define MQTT_ADDR "192.168.0.1"
#define MQTT_PORT 1883
#define MQTT_DATA_TOPIC "records"

//Pin componenti
#define STEPPER_1 D0
#define STEPPER_2 D3
#define STEPPER_3 D4
#define STEPPER_4 D5
#define DC_ENABLE D6
#define LED_PIN 13      //GPIO8   - SD1
#define PROBE_PIN 1     //GPIO1   - TX
#define DHT_PIN 3       //GPIO3   - RX
#define GPS_PIN 15      //GPIO15  - D8
#define ADC_PIN A0       //ADC0    - A0

//Motori
#define STEP_TOTALI 4096
int posizioneCorrenteInStep; //si parte da 0 gradi
int posizioneDaRaggiungere;
long ultimoAggiornamentoStepper;
boolean stepperFermo = true;

//Led di stato
int stato = 0; //0: setup in corso, 1: tutto ok (i dati vengono trasmessi), 2: batteria scarica, altro: errore
#define FREQUENZA_STATO0 500
#define FREQUENZA_STATO2 100
long ultimoAggiornamentoLed;
int ultimoStatoLed;

//Impostazioni invio dati
#define ID_BARCHETTA "4"
#define ID_PROBE "1"
#define ID_DHT11_TEMP "2"
#define ID_DHT11_HUM "3"

//Istanze componenti e dati
OneWire oneWire(PROBE_PIN);
DallasTemperature probe(&oneWire);
DHT dht(DHT_PIN, DHT11);
TinyGPSPlus gpsParser;
SoftwareSerial gps(GPS_PIN, GPS_PIN);
float tempAria, umidAria, tempAcqua, tensione;

//gestione frequenza invio dati
long ultimaVolta;
float frequenzaDati = 0.5; //in Hz

void setup() {
  stato = 0;
  
  pinMode(LED_PIN, OUTPUT);

  //imposto il pin del motore DC
  pinMode(DC_ENABLE, OUTPUT);
  
  setupStepper();
  stopStepper();
  
  //mi connetto al wifi
  connettiWifi();

  connettiMqtt();

  setupSensori();
  
  gps.begin(9600);
}

void loop() {
  //aggiorno i dati del GPS
  aggiornaGps();

  //controllo la connessione
  controllaConnessione();

  aggiornaLed();

  //ogni n secondi leggo i dati e li invio
  if(millis() - ultimaVolta > (1 / frequenzaDati) * 1000) {
    //record and send sensors data
    leggiSensori();
    
    digitalWrite(LED_PIN, LOW);
    inviaDati();
    delay(50);
    digitalWrite(LED_PIN, HIGH);
    
    ultimaVolta = millis();
  }
  
  //controlllo se c'è qualcuno che vuole controllare la barchetta
  if(client) {
    while(client.connected()) {   
      //controllo lo stato del wifi
      controllaConnessione();
      aggiornaLed();
      
      if(client.available()) {
        velocita = "";
        angolo = "";
        direzione = "";

        velocitaC = true;
        angoloC = false;
        direzioneC = false;

        while(client.available() > 0) {
          char c = client.read();
          
          if(c == ',') {
            if(velocitaC) {
              velocitaC = false;
              angoloC = true;
            } else if(angoloC) {
              angoloC = false;
              direzioneC = true;
            }
          } else if(c == ';') {
            muoviElica(angolo.toInt() / 2);
            impostaMotoreDC(velocita.toInt());
            break;
          } else {
            if(velocitaC) {
              velocita += c;
            } else if(angoloC) {
              angolo += c;
            } else if(direzioneC) {
              direzione += c;
            }
          }
          
          aggiornaStepper();
          aggiornaLed();
        }
      }
          
      aggiornaStepper();
    }
    client.stop();
    muoviElica(0);
    impostaMotoreDC(0);
  } else {
    client = server.available();
  }

  aggiornaStepper();

  delay(1);
  mqtt.loop();
}

void controllaConnessione() {
  //controlla la connessione wifi
  if(WiFi.status() != WL_CONNECTED) {
    stato = 3;
    //c'è un errore
    connettiWifi();
  } else {
    stato = 1;
  }

  //controllo la connessione mqtt
  controllaMqtt();
}

void connettiWifi() {
  //provo a connettermi
  WiFi.mode(WIFI_STA);
  WiFi.hostname(MQTT_USR);
  WiFi.begin(WIFI_SSID, WIFI_PSW);

  //aspetto finchè non siamo connessi al wifi
  while(WiFi.status() != WL_CONNECTED) {
    delay(250);
    aggiornaLed();
  }

  //avvio il server tcp
  server.begin();
}

void setupStepper() {
  //imposto i pin dei motori
  pinMode(STEPPER_1, OUTPUT);
  pinMode(STEPPER_2, OUTPUT);
  pinMode(STEPPER_3, OUTPUT);
  pinMode(STEPPER_4, OUTPUT);
}

void muoviElica(int gradi) {
  //accettiamo da -90 a 90 gradi
  if(gradi > 90) gradi = 90;
  else if(gradi < -90) gradi = -90;
  
  //calcolo la posizione da raggiungere
  posizioneDaRaggiungere = gradi * STEP_TOTALI / 360;
}

void aggiornaStepper() {
  if(micros() - ultimoAggiornamentoStepper > 2000) {
    ultimoAggiornamentoStepper = micros();
    if(posizioneDaRaggiungere != posizioneCorrenteInStep) {
      stepperFermo = false;
      //controllo la posizione attuale
      if(posizioneDaRaggiungere > posizioneCorrenteInStep) {
        posizioneCorrenteInStep++;
        stepperSequence((posizioneCorrenteInStep + 1000) % 8);
      } else {
        posizioneCorrenteInStep--;
        stepperSequence((posizioneCorrenteInStep + 1000) % 8);
      }
    } else {
      if(!stepperFermo) {
        stepperFermo = true;
        stopStepper();
      }
    }
  }
}

void stepperSequence(int seqNum) {
  int pin1, pin2, pin3, pin4;
  switch(seqNum){
    case 0: {
      pin1 = 1;
      pin2 = 0;
      pin3 = 0;
      pin4 = 0;
      break;
    }
    case 1: {
      pin1 = 1;
      pin2 = 1;
      pin3 = 0;
      pin4 = 0;
      break;
    }
    case 2: {
      pin1 = 0;
      pin2 = 1;
      pin3 = 0;
      pin4 = 0;
      break;
    }
    case 3: {
      pin1 = 0;
      pin2 = 1;
      pin3 = 1;
      pin4 = 0;
      break;
    } 
    case 4: {
      pin1 = 0;
      pin2 = 0;
      pin3 = 1;
      pin4 = 0;
      break;
    }
    case 5: {
      pin1 = 0;
      pin2 = 0;
      pin3 = 1;
      pin4 = 1;
      break;
    }
    case 6: {
      pin1 = 0;
      pin2 = 0;
      pin3 = 0;
      pin4 = 1;
      break;
    }
    case 7: {
      pin1 = 1;
      pin2 = 0;
      pin3 = 0;
      pin4 = 1;
      break;
    }
    default: {
      pin1 = 0;
      pin2 = 0;
      pin3 = 0;
      pin4 = 0;
      break;
    }
  }
  digitalWrite(STEPPER_1, pin1);
  digitalWrite(STEPPER_2, pin2);
  digitalWrite(STEPPER_3, pin3);
  digitalWrite(STEPPER_4, pin4);
}

void stopStepper() {
  digitalWrite(STEPPER_1, LOW);
  digitalWrite(STEPPER_2, LOW);
  digitalWrite(STEPPER_3, LOW);
  digitalWrite(STEPPER_4, LOW);
}

void aggiornaLed() {
  switch(stato) {
    case 0:
      if(millis() - ultimoAggiornamentoLed > FREQUENZA_STATO0) {
        if(ultimoStatoLed) {
          ultimoStatoLed = 0;
          digitalWrite(LED_PIN, ultimoStatoLed);
        } else {
          ultimoStatoLed = 1;
          digitalWrite(LED_PIN, ultimoStatoLed);
        }
        ultimoAggiornamentoLed = millis();
      }
      break;
    case 1:
      ultimoStatoLed = 1;
      digitalWrite(LED_PIN, ultimoStatoLed);
      break;
    case 2:
      if(millis() - ultimoAggiornamentoLed > FREQUENZA_STATO2) {
        if(ultimoStatoLed) {
          ultimoStatoLed = 0;
          digitalWrite(LED_PIN, ultimoStatoLed);
        } else {
          ultimoStatoLed = 1;
          digitalWrite(LED_PIN, ultimoStatoLed);
        }
        ultimoAggiornamentoLed = millis();
      }
      break;
    default:
      if(millis() - ultimoAggiornamentoLed > FREQUENZA_STATO2) {
        switch(ultimoStatoLed) {
          case 1:
            digitalWrite(LED_PIN, HIGH);
            break;
          case 2:
            digitalWrite(LED_PIN, LOW);
            break;
          case 3:
            digitalWrite(LED_PIN, HIGH);
            break;
          case 4:
            digitalWrite(LED_PIN, LOW);
            break;
          case 5:
            digitalWrite(LED_PIN, LOW);
            break;
        }
        ultimoStatoLed++;
        if(ultimoStatoLed > 5) ultimoStatoLed = 0;
        ultimoAggiornamentoLed = millis();
      }
      break;
  }
}

void impostaMotoreDC(int vel) {
  if(vel > 10) {
    analogWrite(DC_ENABLE, map(vel, 0, 100, 256, 1023));
  } else {
    digitalWrite(DC_ENABLE, LOW);
  }
}

void connettiMqtt() {
  //imposto l'indirizzo del server e la porta
  mqtt.setServer(MQTT_ADDR, MQTT_PORT);

  //provo a connettermi con username e password, se non funziona aspetto 2 secondi e riprovo
  while(!mqtt.connected()) {
    aggiornaLed();
    if(!mqtt.connect(MQTT_USR, MQTT_USR, MQTT_PSW)) delay(2000);
  }
}

void setupSensori() {
  probe.begin();
  dht.begin();
}

void leggiSensori() {
  probe.requestTemperatures();
  tempAcqua = probe.getTempCByIndex(0);
  tempAria = dht.readTemperature();
  umidAria = dht.readHumidity();
  tensione = (float) 0.0058783*analogRead(ADC_PIN);
}

void aggiornaGps() {
  if(gps.available() > 0) {
    while(gps.available() > 0) {
      gpsParser.encode(gps.read());
    }
  }
}

void inviaDati() {
  DynamicJsonDocument record(capacity);
  
  //JsonObject record = doc.createNestedObject("record");
  record["idBarchetta"] = ID_BARCHETTA;
  record["tensione"].set((float) tensione);
  record["latitudine"] = gpsParser.location.lat(); //String(gpsParser.location.lat(), 6); 
  record["longitudine"] = gpsParser.location.lng(); //String(gpsParser.location.lng(), 6);
  record["satelliti"] = gpsParser.satellites.value();
  record["altitudine"] = gpsParser.altitude.meters();
  record["velocita"] = gpsParser.speed.mps();
  record["hdop"] = (float) gpsParser.hdop.value()/100;
  String dateTime = "";
  dateTime += gpsParser.date.year();
  dateTime += "-";
  dateTime += gpsParser.date.month();
  dateTime += "-";
  dateTime += gpsParser.date.day();
  dateTime += " ";
  dateTime += gpsParser.time.hour();
  dateTime += ":";
  dateTime += gpsParser.time.minute();
  dateTime += ":";
  dateTime += gpsParser.time.second(); //2019-02-28 10:10:00
  record["dateTime"] = dateTime;
  
  JsonArray datiSensori = record.createNestedArray("datiSensori");

  if(!isnan(tempAcqua) && tempAcqua != -127) {
    JsonObject datiSensori_0 = datiSensori.createNestedObject();
    datiSensori_0["valore"].set((float) tempAcqua);
    datiSensori_0["idSensore"] = ID_PROBE;
  }
  
  if(!isnan(tempAria)) {
    JsonObject datiSensori_1 = datiSensori.createNestedObject();
    datiSensori_1["valore"].set((float) tempAria);
    datiSensori_1["idSensore"] = ID_DHT11_TEMP;
  }
  
  if(!isnan(umidAria)) {
    JsonObject datiSensori_2 = datiSensori.createNestedObject();
    datiSensori_2["valore"].set((float) umidAria);
    datiSensori_2["idSensore"] = ID_DHT11_HUM;
  }

  String messaggio = "";
  serializeJson(record, messaggio);
  char payload[messaggio.length() + 1];
  messaggio.toCharArray(payload, messaggio.length() + 1);
  
  //send the actual message
  mqtt.publish(MQTT_DATA_TOPIC, payload);
}

void controllaMqtt() {
  if(mqtt.state() != MQTT_CONNECTED) {
    stato = 3;
    //provo a ricollegarmi
    connettiMqtt();
  } else {
    stato = 1;
  }
}

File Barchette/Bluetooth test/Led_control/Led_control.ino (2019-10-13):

#include <BLEDevice.h>
#include <BLEServer.h>
#include <BLEUtils.h>
#include <BLE2902.h>
#include <DHT.h>
#include <OneWire.h>
#include <DallasTemperature.h>
#include <TinyGPS++.h>

#define DHT_PIN 4 //GPIO4
#define DS18B20_PIN 5 // GPIO5

#define FREQUENZA_DATI .5 // Frequenza in Hz
#define MAX_CLIENT_COUNT 2

#define SENSORS_SERVICE_UUID                      "00100001-358C-4B41-9A2B-A2ACE9730461"
#define AIR_TEMPERATURE_CHARACTERISTIC_UUID       "00100002-358C-4B41-9A2B-A2ACE9730461"
#define AIR_HUMIDITY_CHARACTERISTIC_UUID          "00100003-358C-4B41-9A2B-A2ACE9730461"
#define WATER_TEMPERATURE_CHARACTERISTIC_UUID     "00100004-358C-4B41-9A2B-A2ACE9730461"

#define GPS_LOCATION_SERVICE_UUID                 "00200001-358C-4B41-9A2B-A2ACE9730461"
#define GPS_LATITUDE_CHARACTERISTIC_UUID          "00200002-358C-4B41-9A2B-A2ACE9730461"
#define GPS_LONGITUDE_CHARACTERISTIC_UUID         "00200003-358C-4B41-9A2B-A2ACE9730461"
#define GPS_SATELLITES_CHARACTERISTIC_UUID        "00200004-358C-4B41-9A2B-A2ACE9730461"
#define GPS_ALTITUDE_CHARACTERISTIC_UUID          "00200005-358C-4B41-9A2B-A2ACE9730461"
#define GPS_SPEED_CHARACTERISTIC_UUID             "00200006-358C-4B41-9A2B-A2ACE9730461"
#define GPS_HDOP_CHARACTERISTIC_UUID              "00200007-358C-4B41-9A2B-A2ACE9730461"

#define CONTROL_SERVICE_UUID                      "00300001-358C-4B41-9A2B-A2ACE9730461"
#define SPEED_CHARACTERISTIC_UUID                 "00300002-358C-4B41-9A2B-A2ACE9730461"
#define DIRECTION_CHARACTERISTIC_UUID             "00300003-358C-4B41-9A2B-A2ACE9730461"

// Sezione sensori

DHT dht(DHT_PIN, DHT11);
OneWire oneWire(DS18B20_PIN);
DallasTemperature ds18b20(&oneWire);
TinyGPSPlus gpsParser;

float tempAria, tempAcqua;
int umidAria;
float gpsLatitude, gpsLongitude, gpsSpeed, gpsHdop;
int gpsSatellites, gpsAltitude;

// Sezione BLE

BLEServer         *bleServer;
BLEService        *sensorsService;
BLECharacteristic *airTemperatureCharacteristic;
BLECharacteristic *airHumidityCharacteristic;
BLECharacteristic *waterTemperatureCharacteristic;

BLEService        *gpsLocationService;
BLECharacteristic *gpsLatitudeCharacteristic;
BLECharacteristic *gpsLongitudeCharacteristic;
BLECharacteristic *gpsSatellitesCharacteristic;
BLECharacteristic *gpsAltitudeCharacteristic;
BLECharacteristic *gpsSpeedCharacteristic;
BLECharacteristic *gpsHdopCharacteristic;

BLEService        *controlService;
BLECharacteristic *speedCharacteristic;
class SpeedCallbacks: public BLECharacteristicCallbacks {
    void onWrite(BLECharacteristic *pCharacteristic) {
      std::string value = pCharacteristic->getValue();

      if (value.length() > 0) {
        Serial.print("New speed: ");
        for (int i = 0; i < value.length(); i++)
          Serial.print(value[i]);
        Serial.println();
      }
    }
};
BLECharacteristic *directionCharacteristic;
class DirectionCallbacks: public BLECharacteristicCallbacks {
    void onWrite(BLECharacteristic *pCharacteristic) {
      std::string value = pCharacteristic->getValue();

      if (value.length() > 0) {
        Serial.print("New direction: ");
        for (int i = 0; i < value.length(); i++)
          Serial.print(value[i]);
        Serial.println();
      }
    }
};

class ServerCallbacks: public BLEServerCallbacks {
    void onConnect(BLEServer* pServer) {
      Serial.println("Dispositivo connesso");
      Serial.print("Dispositivi connessi: "); Serial.println(bleServer->getConnectedCount());
      if(bleServer->getConnectedCount() < MAX_CLIENT_COUNT) bleServer->startAdvertising(); // Riavvio l'advertising per permetter anche ad altri dispositivi di connettersi, rimuovere per permettere un solo dispositivo alla volta
    };

    void onDisconnect(BLEServer* pServer) {
      Serial.println("Dispositivo disconnesso");
      Serial.print("Dispositivi connessi: "); Serial.println(bleServer->getConnectedCount());
      if(bleServer->getConnectedCount() < MAX_CLIENT_COUNT) bleServer->startAdvertising();
    }
};

void setup() {
  Serial.begin(115200);

  // Preparo i sensori
  dht.begin();
  ds18b20.begin();
  Serial2.begin(9600);
  
  // Avvio il bluetooth
  BLEDevice::init("Barchetta 1");

  // Creo il server BLE
  bleServer = BLEDevice::createServer();
  bleServer->setCallbacks(new ServerCallbacks());

  // Servizio e caratteristiche per i sensori
  sensorsService = bleServer->createService(BLEUUID(SENSORS_SERVICE_UUID), 11);
  
  airTemperatureCharacteristic = sensorsService->createCharacteristic(
    AIR_TEMPERATURE_CHARACTERISTIC_UUID,
    BLECharacteristic::PROPERTY_READ   |
    BLECharacteristic::PROPERTY_NOTIFY
  );
  airTemperatureCharacteristic->addDescriptor(new BLE2902());
  
  airHumidityCharacteristic = sensorsService->createCharacteristic(
    AIR_HUMIDITY_CHARACTERISTIC_UUID,
    BLECharacteristic::PROPERTY_READ   |
    BLECharacteristic::PROPERTY_NOTIFY
  );
  airHumidityCharacteristic->addDescriptor(new BLE2902());

  waterTemperatureCharacteristic = sensorsService->createCharacteristic(
    WATER_TEMPERATURE_CHARACTERISTIC_UUID,
    BLECharacteristic::PROPERTY_READ   |
    BLECharacteristic::PROPERTY_NOTIFY
  );
  waterTemperatureCharacteristic->addDescriptor(new BLE2902());

  // Servizio e caratteristiche per GPS
  gpsLocationService = bleServer->createService(BLEUUID(GPS_LOCATION_SERVICE_UUID), 20);
  
  gpsLatitudeCharacteristic = gpsLocationService->createCharacteristic(
    GPS_LATITUDE_CHARACTERISTIC_UUID,
    BLECharacteristic::PROPERTY_READ   |
    BLECharacteristic::PROPERTY_NOTIFY
  );
  gpsLatitudeCharacteristic->addDescriptor(new BLE2902());
  
  gpsLongitudeCharacteristic = gpsLocationService->createCharacteristic(
    GPS_LONGITUDE_CHARACTERISTIC_UUID,
    BLECharacteristic::PROPERTY_READ   |
    BLECharacteristic::PROPERTY_NOTIFY
  );
  gpsLongitudeCharacteristic->addDescriptor(new BLE2902());
  
  gpsSatellitesCharacteristic = gpsLocationService->createCharacteristic(
    GPS_SATELLITES_CHARACTERISTIC_UUID,
    BLECharacteristic::PROPERTY_READ   |
    BLECharacteristic::PROPERTY_NOTIFY
  );
  gpsSatellitesCharacteristic->addDescriptor(new BLE2902());
  
  gpsAltitudeCharacteristic = gpsLocationService->createCharacteristic(
    GPS_ALTITUDE_CHARACTERISTIC_UUID,
    BLECharacteristic::PROPERTY_READ   |
    BLECharacteristic::PROPERTY_NOTIFY
  );
  gpsAltitudeCharacteristic->addDescriptor(new BLE2902());
  
  gpsSpeedCharacteristic = gpsLocationService->createCharacteristic(
    GPS_SPEED_CHARACTERISTIC_UUID,
    BLECharacteristic::PROPERTY_READ   |
    BLECharacteristic::PROPERTY_NOTIFY
  );
  gpsSpeedCharacteristic->addDescriptor(new BLE2902());
  
  gpsHdopCharacteristic = gpsLocationService->createCharacteristic(
    GPS_HDOP_CHARACTERISTIC_UUID,
    BLECharacteristic::PROPERTY_READ   |
    BLECharacteristic::PROPERTY_NOTIFY
  );
  gpsHdopCharacteristic->addDescriptor(new BLE2902());
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

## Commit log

2019-03-07 Aggiornato lo scroll e le unità di misura
2019-03-28 Penultima revisione
    [Asse motore.stl, Bandierina.stl, Contatto batterie AAA pt1.stl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]
2019-05-03 Sistemato il link per il vide del modello
2019-10-12 Esp32 ora invia la temperatura dell'aria tramite BLE (lettura e notifiche)
2019-10-13 Web App funzionante, manca la grafica
